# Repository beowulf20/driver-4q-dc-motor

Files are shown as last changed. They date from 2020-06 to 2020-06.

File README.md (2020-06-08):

# Projeto Driver 4Q 2020/1

## Especificação
- Acionamento do motor [M 210 1K2 24V](http://motron.com.br/produtos/210/curvas/m210-iverln-1k2-24v.pdf) 

## Abrangência
- Fonte Primária (220Vac)
> Trafo + Retificador + Filtro Capacitivo (ou fonte chaveada)
- Circuito Modulador PWM (escolher CI comercial ou microcontrolador com software)
- Driver
> Ponte comercial ou MOSFET (incluir driver do gate)

# Referências

[Using Spice To Model DC Motors](https://www.precisionmicrodrives.com/content/ab-025-using-spice-to-model-dc-motors/)
[LTSpice Tutorial - Modeling a DC brushed motor](https://www.youtube.com/watch?v=Wc4XzTrWSpo)

[M210 1K2 24V Datasheet](docs/m210-iverln-1k2-24v.pdf)

[Guia Prático Proteção de Motores](docs/protecao_motores.pdf)

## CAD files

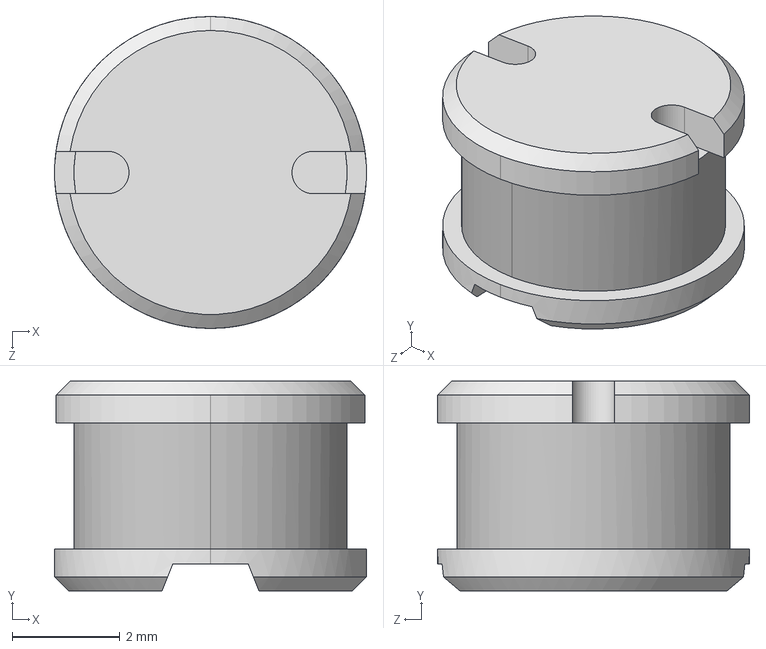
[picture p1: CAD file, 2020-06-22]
kicad 3d models/User Library-SDR0603.step
5.80 x 3.90 x 5.80 mm

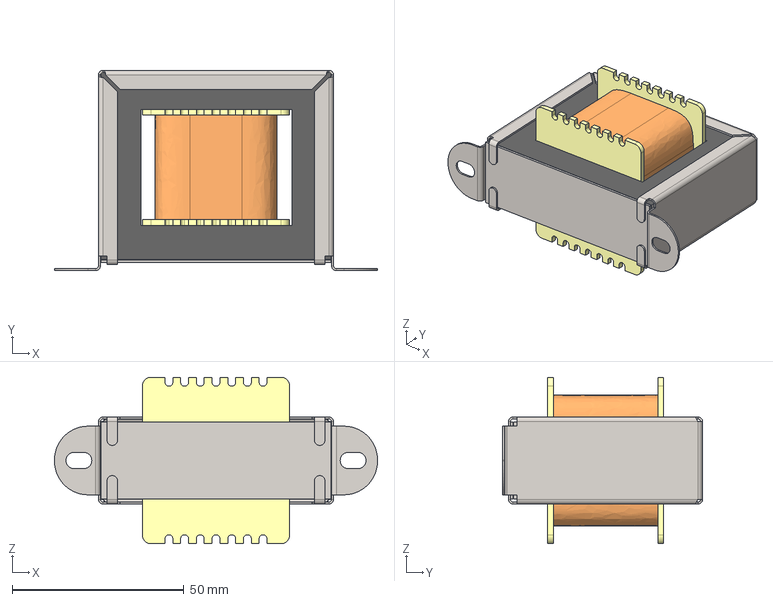
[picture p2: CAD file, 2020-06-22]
kicad 3d models/TRANSFORMER_2.step
94.1 x 58.4 x 48.5 mm

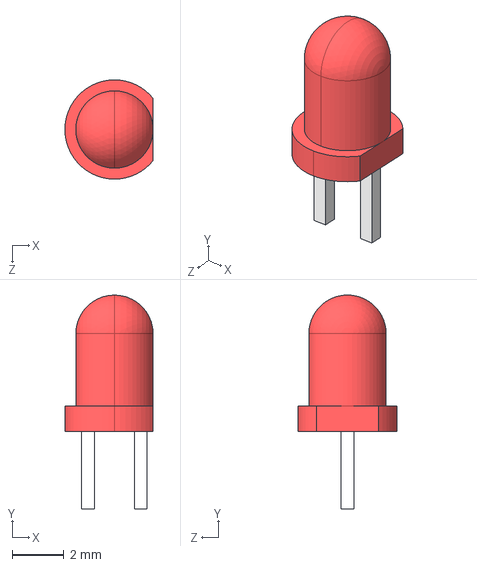
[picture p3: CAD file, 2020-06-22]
kicad 3d models/LED-C-3mm-R.step
3.43 x 8.30 x 3.85 mm

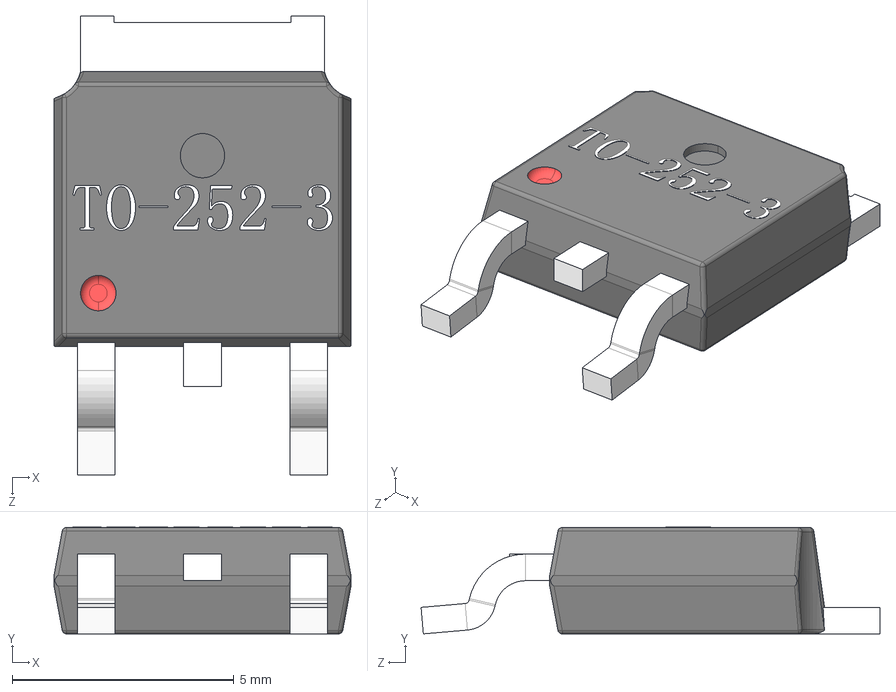
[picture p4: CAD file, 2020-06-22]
kicad 3d models/TO-252-3.step
6.70 x 2.41 x 10.4 mm

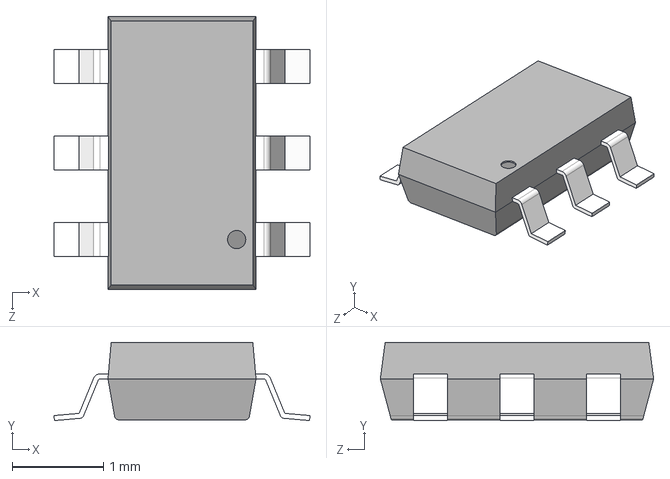
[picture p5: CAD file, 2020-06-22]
kicad 3d models/TSOT-23-6.step
2.81 x 0.857 x 3.00 mm

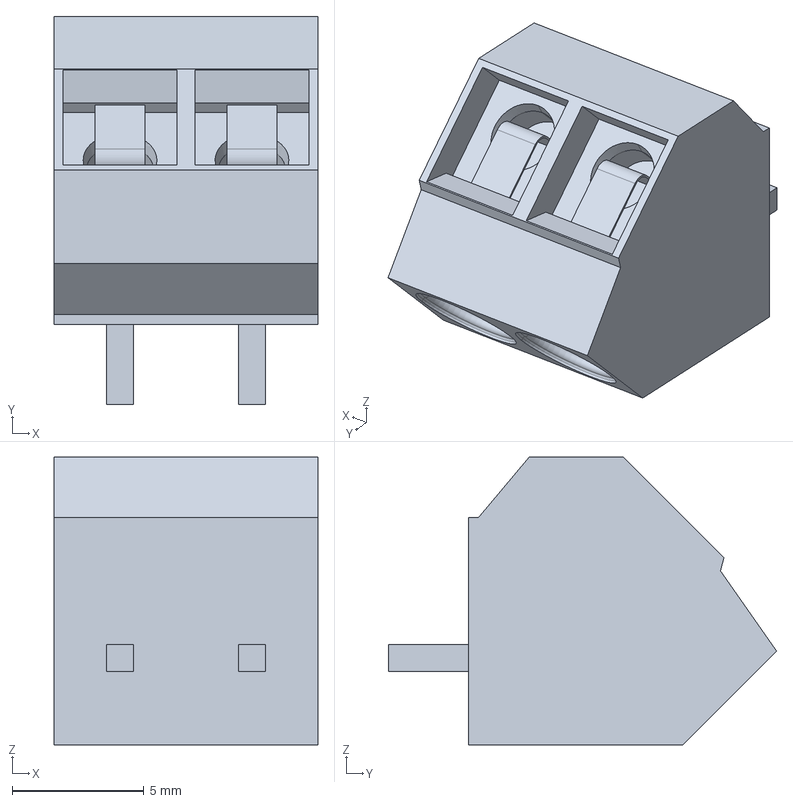
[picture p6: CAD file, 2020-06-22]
kicad 3d models/Terminal Block 5mm Pitch 45deg - Molex .stp
10.0 x 14.7 x 10.9 mm

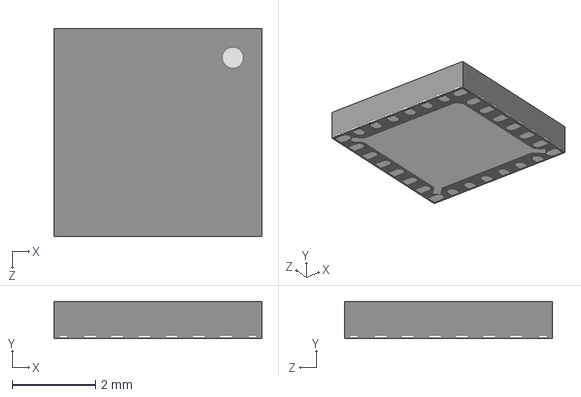
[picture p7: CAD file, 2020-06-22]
kicad 3d models/QFN 24.step
5.00 x 0.9 x 5.00 mm

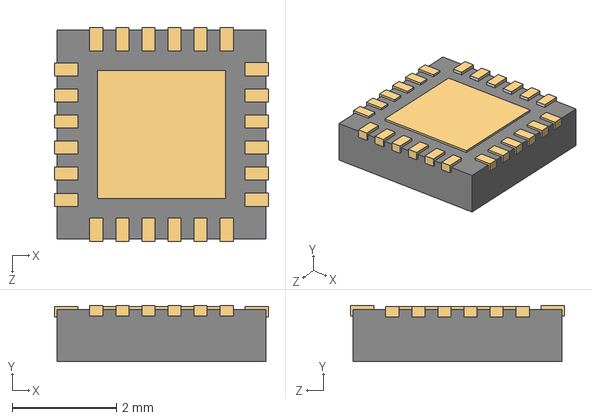
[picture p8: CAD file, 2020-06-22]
kicad 3d models/VQFN-24.step
4.10 x 1.07 x 4.10 mm

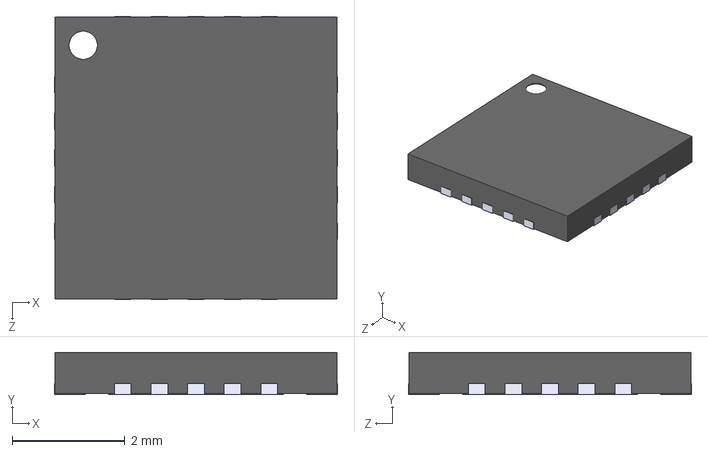
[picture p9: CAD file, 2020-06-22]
kicad 3d models/Maxim_TQFN20.step
5.02 x 0.75 x 5.02 mm

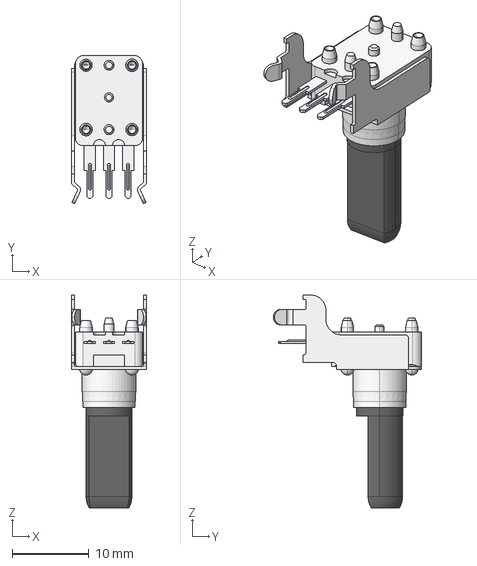
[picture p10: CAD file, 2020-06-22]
kicad 3d models/RK09D1110C0R.STEP
9.80 x 19.4 x 27.8 mm

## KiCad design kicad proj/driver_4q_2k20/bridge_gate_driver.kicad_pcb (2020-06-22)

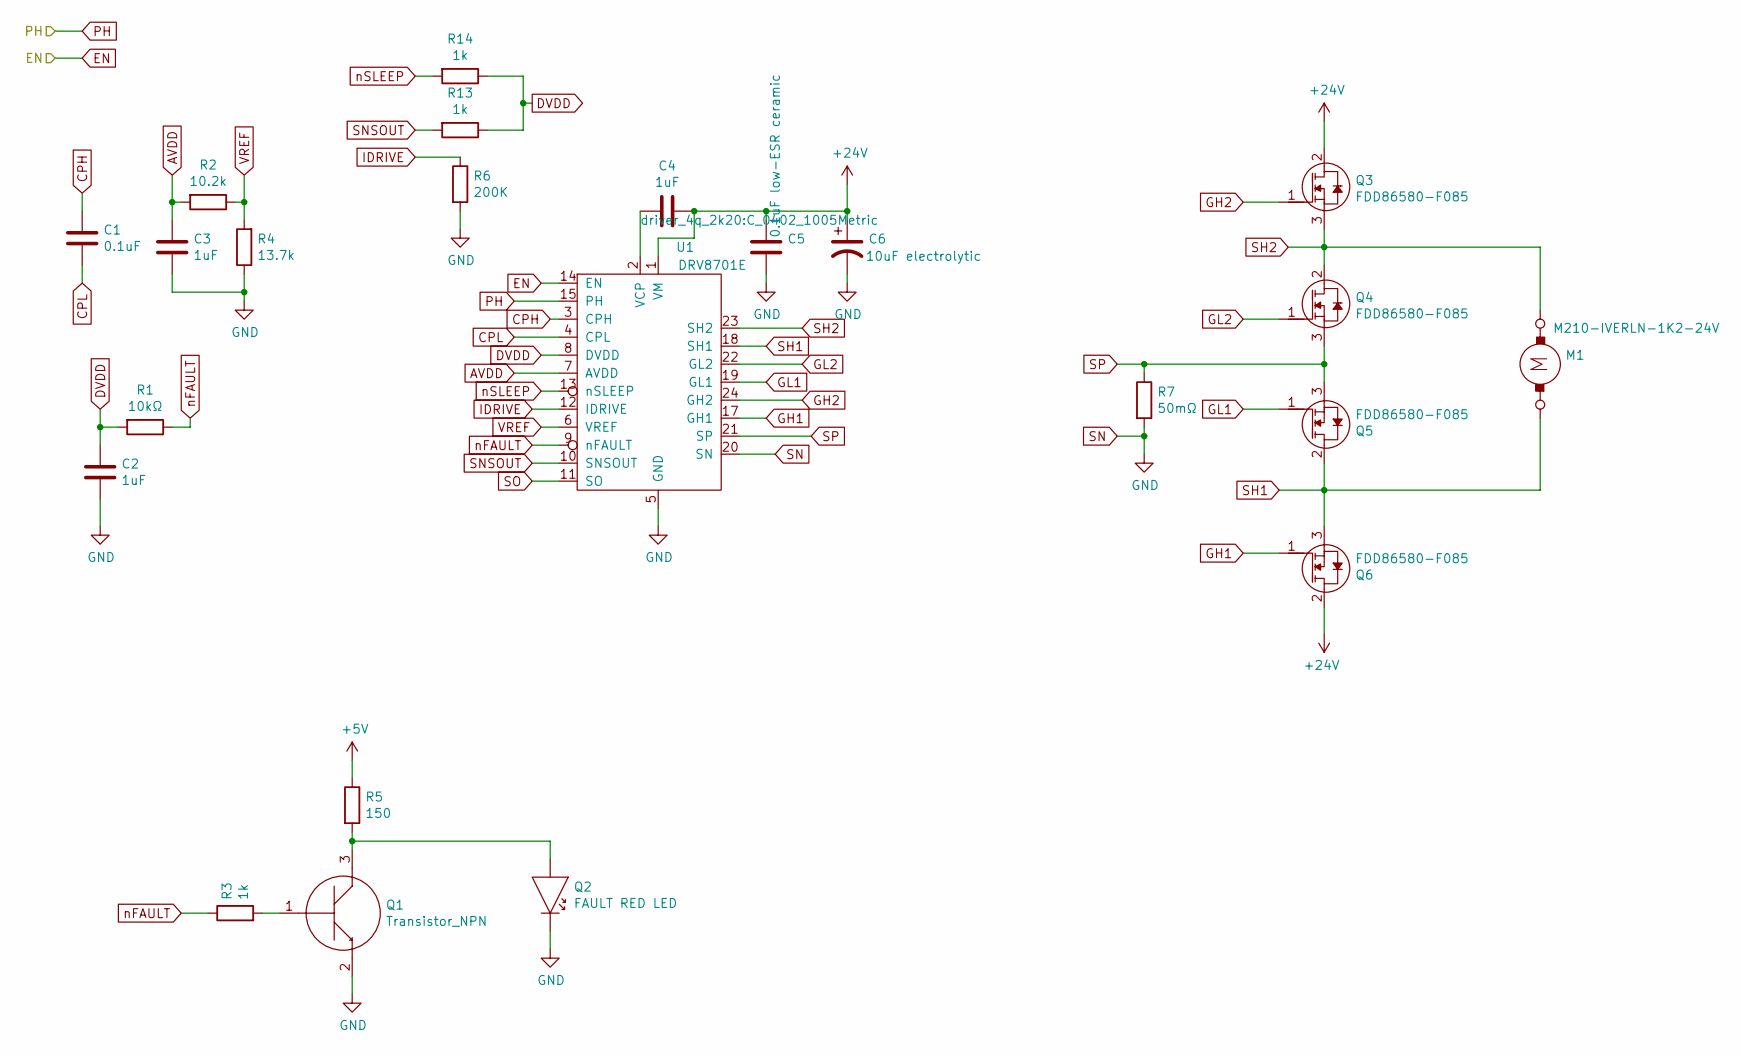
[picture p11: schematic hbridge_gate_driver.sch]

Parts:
C1: 0.1uF; C_0402_1005Metric
C2, C3, C4: 1uF; C_0402_1005Metric
C5: 0.1uF low-ESR ceramic; C_0402_1005Metric
C6: 10uF electrolytic; CP_Radial_D5.0mm_P2.00mm
M1: M210-IVERLN-1K2-24V; 395430203
Q1: Transistor_NPN; SOT-23
Q2: FAULT RED LED; LTL-10224W-RED
Q3, Q4, Q5, Q6: FDD86580-F085; TO-252-3_TabPin2
R1: 10kΩ; R_0402_1005Metric
R2: 10.2k; R_0402_1005Metric
R3: 1k; C_0402_1005Metric
R4: 13.7k; R_0402_1005Metric
R5: 150; C_0402_1005Metric
R6: 200K; C_0402_1005Metric
R7: 50mΩ; R_0402_1005Metric
R13, R14: 1k; R_0402_1005Metric
U1: DRV8701E; DRV8701

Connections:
24V: C4.2, C5.2, C6.1, Q3.2 (D), Q6.2 (D), U1.1 (VM); also elsewhere on the board
+5V: R5.1; also elsewhere on the board
AVDD: C3.1, R2.2, U1.7 (AVDD)
CPH: C1.2, U1.3 (CPH)
CPL: C1.1, U1.4 (CPL)
DIR: U1.15 (PH); also elsewhere on the board
DVDD: C2.1, R1.2, R13.1, R14.1, U1.8 (DVDD)
EN: U1.14 (EN); also elsewhere on the board
GH1: Q6.1 (G), U1.17 (GH1)
GH2: Q3.1 (G), U1.24 (GH2)
GL1: Q5.1 (G), U1.19 (GL1)
GL2: Q4.1 (G), U1.22 (GL2)
GND: C2.2, C3.2, C5.1, C6.2, Q1.2, Q2.2, R4.1, R6.2, R7.2, U1.5 (GND), U1.20 (SN); also elsewhere on the board
IDRIVE: R6.1, U1.12 (IDRIVE)
unnamed: C4.1, U1.2 (VCP)
unnamed: Q1.1, R3.2
unnamed: Q1.3, Q2.1 (K), R5.2
SH1: M1.2, Q5.2 (D), Q6.3 (S), U1.18 (SH1)
SH2: M1.1, Q3.3 (S), Q4.2 (D), U1.23 (SH2)
SNSOUT: R13.2, U1.10 (SNSOUT)
SO: U1.11 (SO)
SP: Q4.3 (S), Q5.3 (S), R7.1, U1.21 (SP)
VREF: R2.1, R4.2, U1.6 (VREF)
nFAULT: R1.1, R3.1, U1.9 (nFAULT)
nSLEEP: R14.2, U1.13 (nSLEEP)

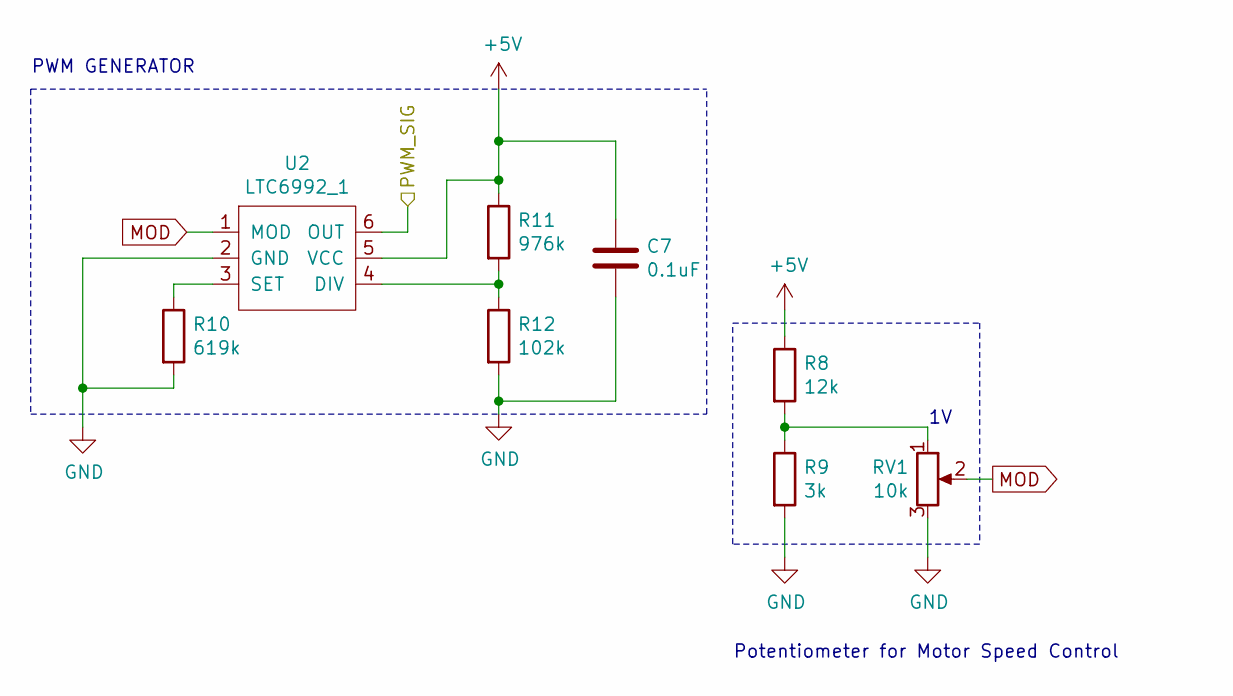
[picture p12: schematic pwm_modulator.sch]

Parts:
C7: 0.1uF; C_0402_1005Metric
R8: 12k; R_0402_1005Metric
R9: 3k; R_0402_1005Metric
R10: 619k; R_0402_1005Metric
R11: 976k; R_0402_1005Metric
R12: 102k; R_0402_1005Metric
RV1: 10k; RK09D111
U2: LTC6992_1; TSOT-23-6

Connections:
+5V: C7.1, R8.1, R11.1, U2.5 (VCC); also elsewhere on the board
EN: U2.6 (OUT); also elsewhere on the board
GND: C7.2, R9.2, R10.2, R12.2, RV1.3, U2.2 (GND); also elsewhere on the board
MOD: RV1.2, U2.1 (MOD)
unnamed: R8.2, R9.1, RV1.1
unnamed: R10.1, U2.3 (SET)
unnamed: R11.2, R12.1, U2.4 (DIV)

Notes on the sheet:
Potentiometer for Motor Speed Control
PWM GENERATOR

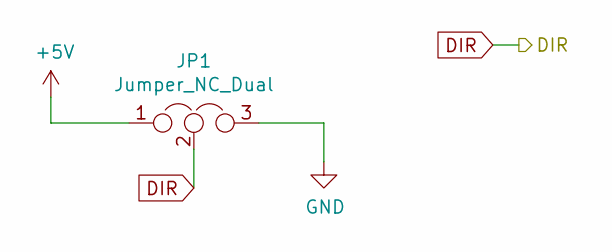
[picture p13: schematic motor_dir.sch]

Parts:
JP1: Jumper_NC_Dual; PinHeader_1x03_P1.27mm_Vertical

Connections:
+5V: JP1.1; also elsewhere on the board
DIR: JP1.2; also elsewhere on the board
GND: JP1.3; also elsewhere on the board

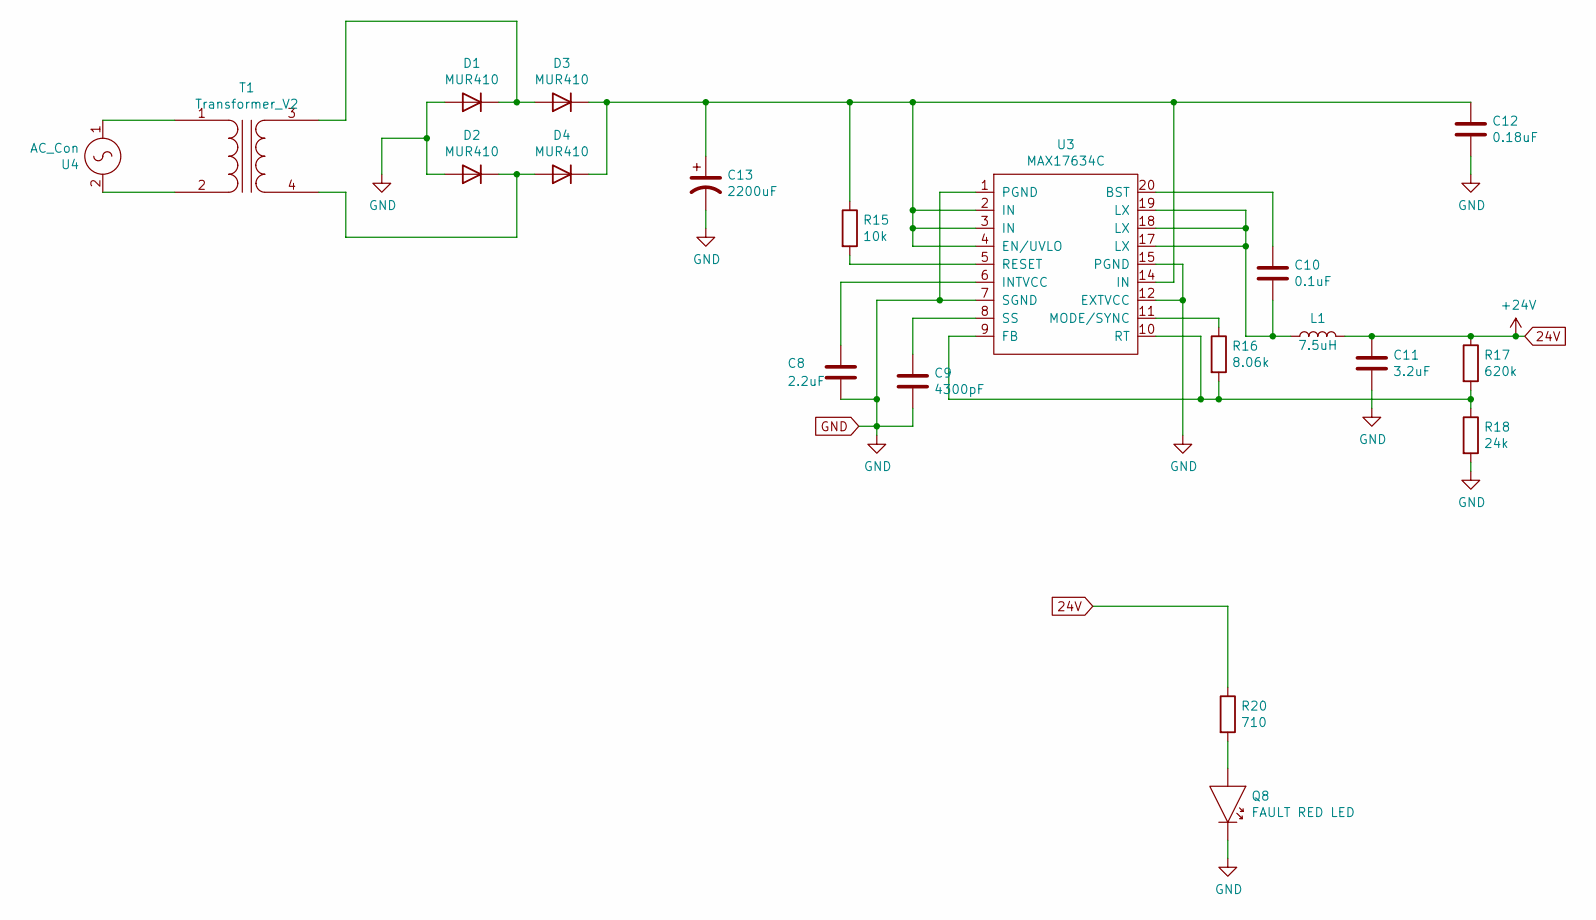
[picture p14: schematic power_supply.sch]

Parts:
C8: 2.2uF; C_0402_1005Metric
C9: 4300pF; C_0402_1005Metric
C10: 0.1uF; C_0402_1005Metric
C11: 3.2uF; C_0402_1005Metric
C12: 0.18uF; C_0402_1005Metric
C13: 2200uF; CP_Radial_D5.0mm_P2.00mm
D1, D2, D3, D4: MUR410; D_DO-41_SOD81_P10.16mm_Horizontal
L1: 7.5uH; L_TracoPower_TCK-047_5.2x5.8mm
Q8: FAULT RED LED; LTL-10224W-RED
R15: 10k; R_0402_1005Metric
R16: 8.06k; R_0402_1005Metric
R17: 620k; R_0402_1005Metric
R18: 24k; R_0402_1005Metric
R20: 710; C_0402_1005Metric
T1: Transformer_V2; Transformer_96x87
U3: MAX17634C; TQFN-20-1EP_5x5mm_P0.65mm_EP3.1x3.1mm
U4: AC_Con; 395430203

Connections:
24V: C11.1, L1.2, R17.1, R20.1; also elsewhere on the board
GND: C8.2, C9.2, C11.2, C12.2, C13.2, D1.2 (A), D2.2 (A), Q8.2, R18.2, U3.1 (PGND), U3.7 (SGND), U3.12 (EXTVCC), U3.15 (PGND); also elsewhere on the board
unnamed: C8.1, U3.6 (INTVCC)
unnamed: C9.1, U3.8 (SS)
unnamed: C10.1, U3.20 (BST)
unnamed: C10.2, L1.1, U3.17 (LX), U3.18 (LX), U3.19 (LX)
unnamed: C12.1, C13.1, D3.1 (K), D4.1 (K), R15.1, U3.2 (IN), U3.3 (IN), U3.4 (EN/UVLO), U3.14 (IN)
unnamed: D1.1 (K), D3.2 (A), T1.3 (SB)
unnamed: D2.1 (K), D4.2 (A), T1.4 (SA)
unnamed: Q8.1 (K), R20.2
unnamed: R15.2, U3.5 (RESET)
unnamed: R16.1, U3.11 (MODE/SYNC)
unnamed: R16.2, R17.2, R18.1, U3.9 (FB), U3.10 (RT)
unnamed: T1.1 (AA), U4.1
unnamed: T1.2 (AB), U4.2

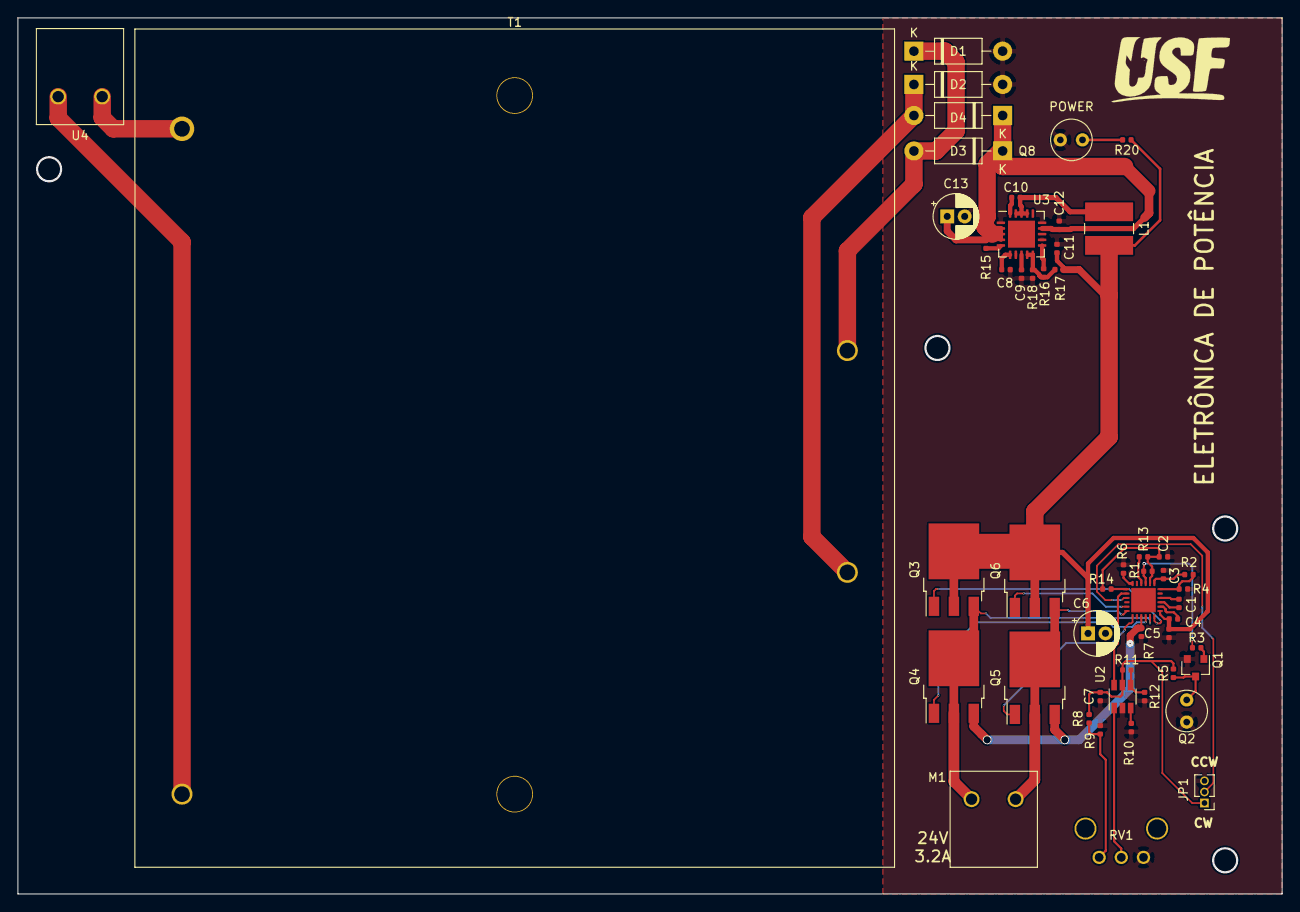
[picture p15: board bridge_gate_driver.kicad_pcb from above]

Board: 2 copper layers, 144.8 x 100.3 mm, 52 parts (0 on the bottom side), 41 nets.

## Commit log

2020-06-08 circuito com gate driver + ponte H + modulador pwm
    [bridge_gate_driver.kicad_pcb, bridge_gate_driver.sch, hbridge_gate_driver.sch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]
2020-06-22 adicionado arquivos step, docs e footprints
    [LED-C-3mm-R.step, Maxim_TQFN20.step, QFN 24.step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]
2020-06-22 added power supply and new transformer
    [TRANSFORMER_2.step, User Library-SDR0603.step, bridge_gate_driver.kicad_pcb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]
